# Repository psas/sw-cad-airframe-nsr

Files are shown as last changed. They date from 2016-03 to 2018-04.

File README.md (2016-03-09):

# Nosecone Separation Ring: The NSR

Solid Works CAD files and history of the nosecone separation ring

See https://github.com/psas/sw-cad-common#psas-solidworks-setup-and-use-procedures for procedures on using github for Solidworks files

## Documentation

Old docs from ancient wiki:

### <http://psas.pdx.edu/LV2cNoseconeSeperationRing/>

 - Drop test: <http://psas.pdx.edu/news/2009-04-19/>
 - Early deploy tests: <http://psas.pdx.edu/news/2009-03-15/>

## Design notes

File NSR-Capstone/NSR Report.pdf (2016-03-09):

# Nose Cone Separation Ring for LV3 High Altitude Sounding

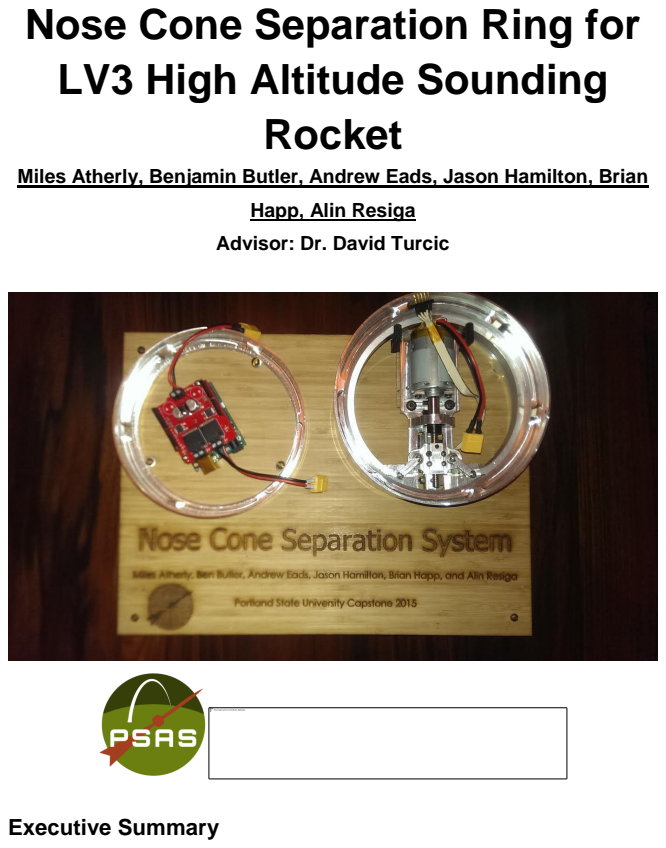
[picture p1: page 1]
Rocket; Executive Summary

Miles Atherly, Benjamin Butler, Andrew Eads, Jason Hamilton, Brian

Happ, Alin Resiga
Advisor: Dr. David Turcic

An electro-mechanical Nosecone Separation Ring (NSR) system was developed for

Portland State Aerospace Society (PSAS). The electro-mechanical NSR will replace

PSAS’ current NSR mechanism, which uses a bonding agent and gunpowder charges.

The new NSR will address several shortcomings exhibited by the current separation

device.

The electro-mechanical NSR uses a DC motor, linear guide rail, ¼-16 ACME power

screw, and relative motion arms, guide pins, and rails to actuate an aluminum v-shaped

clamping band over two angled surfaces A wave spring, which provides a kickoff force

upon separation, is inlayed into a groove in the larger (male) coupling ring. Currently,

the prototype NSR is controlled by pulse width modulation (PWM) via an Arduino Uno

R3. Two limit switches control fore and aft travel of the sled during actuation, and cut

the power to the motor. In its current design state, the NSR is capable of deploying in

less than 63 milliseconds.

Physical testing, finite element analysis, and mathematical models were used to verify

reliability of critical components in the new NSR system. The most critical component,

which also bears the highest stress during actuation, is the aluminum clamping band.

The design of the band was optimized so that it has a minimum factor of safety of 1.67

throughout the actuation.

Table of Contents | Page
1.0 | Introduction | X
2.0 | Mission Statement | X
3.0 | Main Design requirements | X
4.0 | Top-Level Design Decision

5.0 | Final Design | X
6.0 | Evaluations of Components
6.1. V-Band Sizing and Analysis
6.2. Clamped Surface Analysis
6.3. | Motor Sizing | X
7.0 | Evaluations as Related to PDS | X
8.0 | Conclusions and Recommendations

Acknowledgements

Bibliography

Appendix A: Detailed Design

Appendix B: DFMEA on V-band

Appendix C: Potential Yielding at Critical Point

Appendix D: Bill of Materials

Appendix E: Analysis Based Design Decisions

Appendix F Assembly Instructions

Appendix G: Drawings

## 1.0 Introduction

Portland State Aerospace Society (PSAS) was founded in 1997 with the goal of putting

a nano-satellite into orbit. PSAS is in the process of building their third sounding rocket,

and is redesigning several aspects of this rocket, including the nose cone separation

mechanism. Currently, the nose cone is adhered to the main body of the rocket with

epoxy. A small amount of gunpowder is deposited throughout a cavity between the

nose cone and body. At apogee, the gunpowder is ignited via electric matches,

breaking the bond of the epoxy. An internal plunger assembly then pushes the nose cone off the rocket, deploying the parachute. This separation method is not easily

testable, but does allow the rocket to be recovered and reused. PSAS would like an

easily testable, reliable, and more efficient way of releasing the nose cone and

deploying the parachute. Ideally, the new parachute deployment mechanism would be

easy to reset and not use any consumables, such as gunpowder.

Four main separation mechanisms were used to draw ideas from. A Marmon clamp, a LightbandTM, gas actuated pins, and an electromagnetic lock. An electro-mechanical

device similar to the Marmon Clamp, and the V-Band, was chosen for its simplicity and

reliability. The design relies on the expansion and contraction of an angled band to

clamp the upper and lower rings of the rocket together. This device increases the

diameter of the clamping band using a power screw driven by a motor. Since the power

screw is self-locking, the two rings stay clamped without additional power. The motor

reverses the direction of the power screw, and the rings become unclamped in under 63

milliseconds. The electro-mechanical NSR meets all of the design requirements; it is

easily resettable, easily testable, and will withstand the forces it will experience in flight.

## 2.0 Mission Statement

The mission of the NSR team was to design and prototype a device that will facilitate

the separation of the nose cone from the main body of the rocket. The device needs to

be easily testable, resettable, and have a failure rate of less than one percent. The

device must not impede the parachute deployment, and needs to be completed by

June, 5, 2015 with a budget of $3,000.

## 3.0 Main Design Requirements

The current NSR cannot be tested without firing the gunpowder charges which makes it

difficult to predict if the separation ring has been prepared correctly before launch. The epoxy used to bind the nose cone to the body takes several hours to cure, so if any

problems are detected before launch they cannot be corrected on the same day. PSAS

would like to replace their existing NSR with an electro-mechanical device that can be

tested, easily reset, and have a verifiable failure rate of less than one percent. This

would allow them to check the NSR mechanism on launch days. If the device were to

fail, it needs to fail in the closed position (i.e.-the nose cone remains attached to the

airframe in the event of system failure). This is significantly safer than failing in the open

position (i.e- the nose cone is detached from the airframe in the event of system failure)

The NSR should use no more than 5W of standby power and no more than 50W of

power to actuate from the main battery. The device also needs to be operable in a

vacuum, and withstand a tensile force of 250lb PSAS requested, but did not require

that the design of the NSR be modular and scalable so that it can be adapted for stage

release applications and for larger diameter rockets in the future.

## 4.0 Top-Level Design Decision

The three main concepts that were pursued were an electro-mechanical device driven

by a stepper motor, a compressed gas powered 4- pin actuator, and an electromagnetic

lock. The gas powered 4-pin actuator was discarded due to difficulties designing it to fail

in a closed position. An electromagnetic lock design was quickly discarded because the

magnets could be damaged upon touchdown impact. Ultimately, the decision was made

to use a clamp similar to the V-band and Marmon clamp driven by a DC stepper motor.

Later, the stepper motor was replaced with a brushed DC motor as it is easier to

manipulate, can be over-driven, and will satisfy the speed and power requirements of

the proposed design.

From the external and internal search, a concept scoring matrix was used to decide

between alternative ideas. The results are summarized in Table 1. The V-band has the

highest score, and was used as a starting point for the NSR design.

Table 1. Concept Scoring Matrix: Larger numbers correspond to more desireable qualities

| V-band | LightbandTM | Gas Actuated Pins | Electromagnetic
Speed | 3 | 3 | 4 | 5
Manufacturing Complexity | 4 | 3 | 3 | 2
Power System | 4 | 4 | 2 | 2
Binding Risk | 4 | 3 | 2 | 4
Totals | 15 | 13 | 11 | 13

The primary reason for designing a mechanism similar to the V-band instead of something more similar to the LightbandTM was due to manufacturing complexity. The

LightbandTM uses a series of right angle clamps to hold down the upper ring. These

clamps are fixed to the bottom with a shear pin. Creating this design would involve

sourcing or machining eight to ten of these right angle clamps, and designing a way to

fixture them to the lower ring. Having all of these components might also increase the

risk of loading failure. For example, the shear pins could break or the top part of the

right angle clamp could shear off. The decision was also made to clamp from the inside

instead of the more traditional style of clamping from the outside to keep the rocket as

aerodynamic as possible. Figure 1 is a cut-away model of the design where some of

the design aspects are seen..

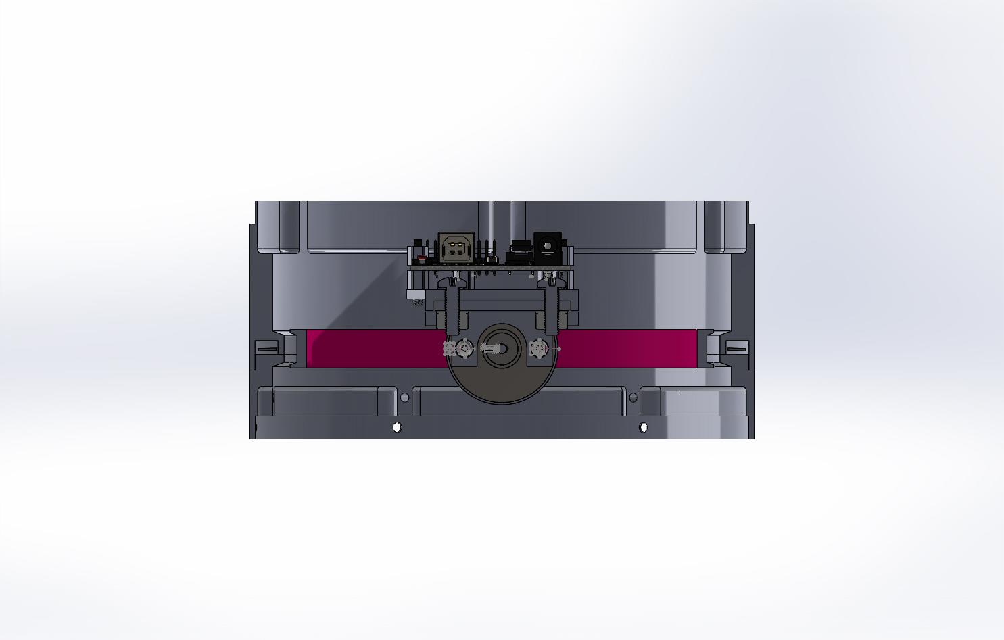
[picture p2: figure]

Figure 1- An isometric cut-away view of the initial design proposal. The design incorporates aspects of both the Marmon Clamping System and the LightbandTM separation device.

The NSR design utilizes an internal inverted marmon clamp. The actuation of the inverted marmon clamp works similarly to the LightbandTM in that the actuation is started

by translating rotational motion from a DC motor into linear motion. The similarities

between the two devices end there, as the NSR’s clamping mechanism significantly differs from that of the LightbandTM.

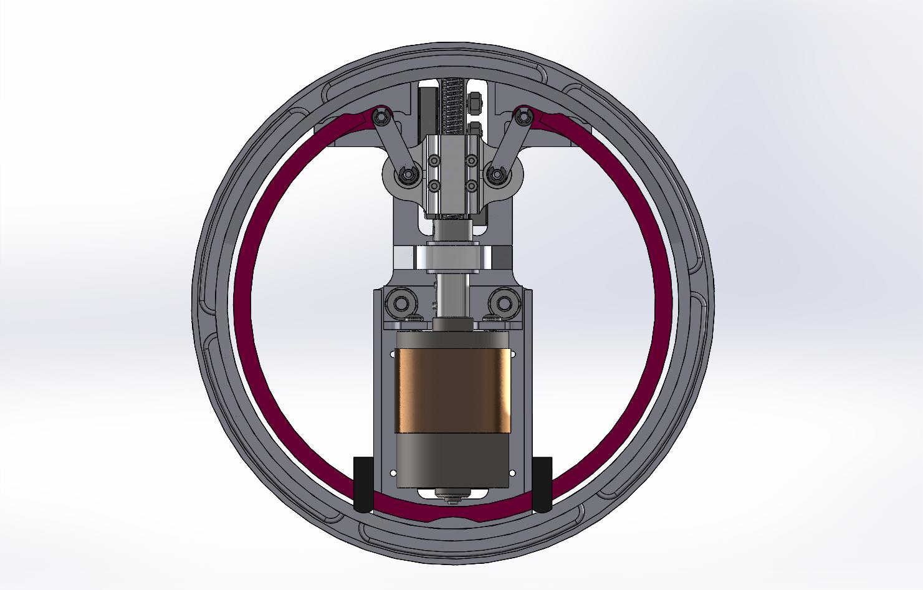
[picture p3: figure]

Figure 2- Top down view of the separation mechanism.

## 5.0 Final Design

The purpose of the mechanism is to provide a clamping force from the V-band

simultaneously to the upper and lower rings to hold the nose cone to the rocket during

flight. Then, at the desired point in flight, release the nose cone and deploy the

parachutes by rapidly contracting the V-band. The nose cone is attached to the upper

coupling ring (female) and the main body of the rocket is attached to the lower coupling

ring (male).

The NSR mechanism is powered independently by an 11.1 V Lithium Polymer

battery. Actuation is started by sending a signal from the flight computer to the control board which powers the motor and drives the V-band to either an open or closed

position. The power screw rides on and is supported by the journal and a pair of needle

thrust bearings. The sled rides back and forth along the power screw, which provides

two important functions; direct horizontal motion for sliding the V-band forward or back

to either clamp or release the nose cone, and to actuate the relative motion arms to

open or contract the V-band.

During the clamping or unclamping sequence, the sled will contact one of two

limit switches mounted under the device. The limit switches signal the control board to

stop the motor and end the actuation sequence. The actuator is attached to the upper,

larger, coupling which will be attached to the nose cone. Upon deployment, the

actuator will separate from the rocket body with the nose cone, allowing plenty of space

for the drogue and main parachutes to deploy through. Figure 3 is a bottom up view of

the complete NSR mechanism. Not pictured are the arduino and the battery.

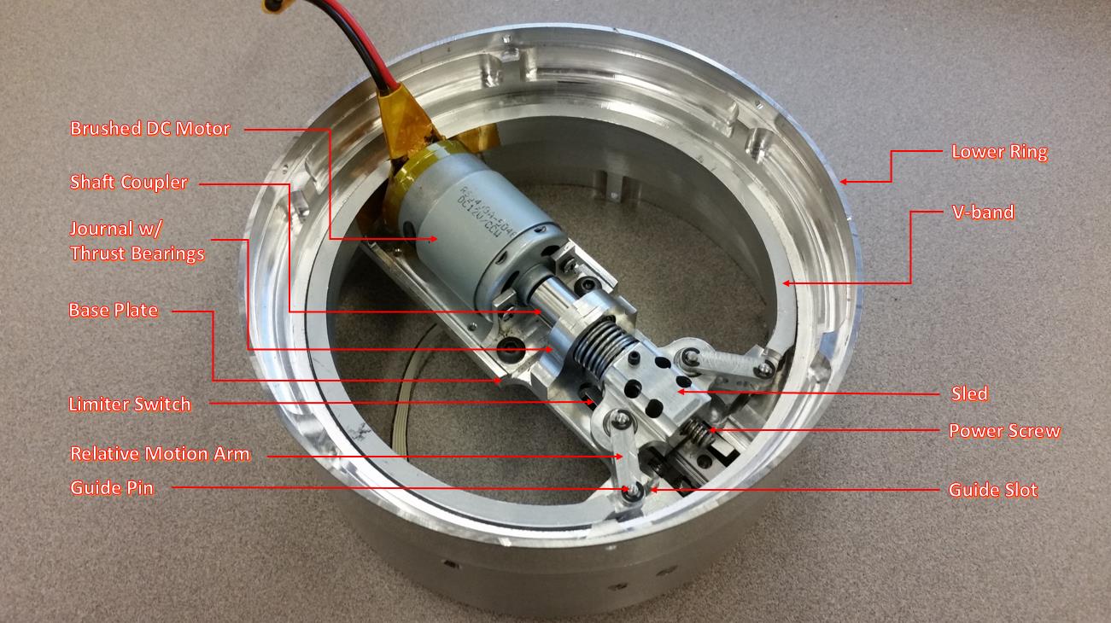
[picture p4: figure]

Figure 3: A bottom up view of the complete NSR assembly.

The NSR components are a combination of in-house custom manufactured components

and prefabricated outsourced components. The in-house manufactured components include both coupling rings, V-band, journal, shaft coupler, sled, motor mount, dowel

pins, male indexing tabs, and actuator arms. The outsourced parts include the power

screw, thrust bearings, 7mm guide rail, 7mm carriage, motor, control board, LiPo

battery, wave spring, and all fasteners.

## 6.0 Evaluation of Components

After the final design concept was approved, three major design points of the NSR were

evaluated. The three design points are the V-band, the clamped surface area of the

coupling rings, and the power requirements of the system.

## 6.1 V-Band Sizing and Analysis

A mathematical model constructed using Castigliano’s theorem, shown in Appendix

E,shows that the force required to displace the tabs of the band depends heavily on the

radius of curvature and the cross-sectional area of the band. The force required to

displace the band will be reduced by increasing the radius of curvature of the neutral

axis, or by decreasing the cross-sectional area of the band. The original V-band design

required a load of 10 lbf per side (20 lbf total) to achieve a net displacement of 0.8 in.

To determine the stress present in the displaced state of the V-band, an FEA model of

the band was built and subjected to a similar load. Meshing properties of the FEA

model were adjusted until the force and displacement parameters of the FEA model

resembled the force and displacement parameters for the mathematical model.

Additionally, a physical experiment was performed in order to validate the results of both

the FEA and the mathematical mode, shown in Appendix C. Results from the physical

experiment matched results from the FEA model and the mathematical model closely,

and the FEA model was deemed as a viable design tool for optimizing V-band

parameters.

FEA analysis of the original V-band exhibited a maximum stress value of 36.98 kpsi

located on the back side of the band on the lip of the clamping surface illustrated in

Figure 4. Since the yield strength of 6061-T6 aluminum is 40 kpsi, the original V-band

design had a factor of safety of 1.08 in its deployed state. A design revision of the V-

band was done in order to increase the factor of safety of the band in the deployed state

as well as decrease the force required for displacement. FEA was used as the primary

design tool in this process.

The cross-sectional area of the V-band was thinned out significantly by removing

material from the web and the lips of the clamping surface. The center of the V-channel

was held constant in order to shift the radial distance of the neutral axis outwards.

Thinning the web and removing material from the lips of the clamping surface reduced

the force required to displace the band from 20 lbf to 6.6 lbf, but did not significantly

reduce the maximum observed stress value. 1.5 in diameter relief cut was added to the

back wall of the V-band where the maximum stress was observed. The addition of the

relief cut reduced the observed stress to 23.92 kpsi and increased the factor of safety to

1.67. The completely revised V-band is seen in Fig. 5 and shows the maximum stress

concentration location, and magnitude relative to yield strength of the material.

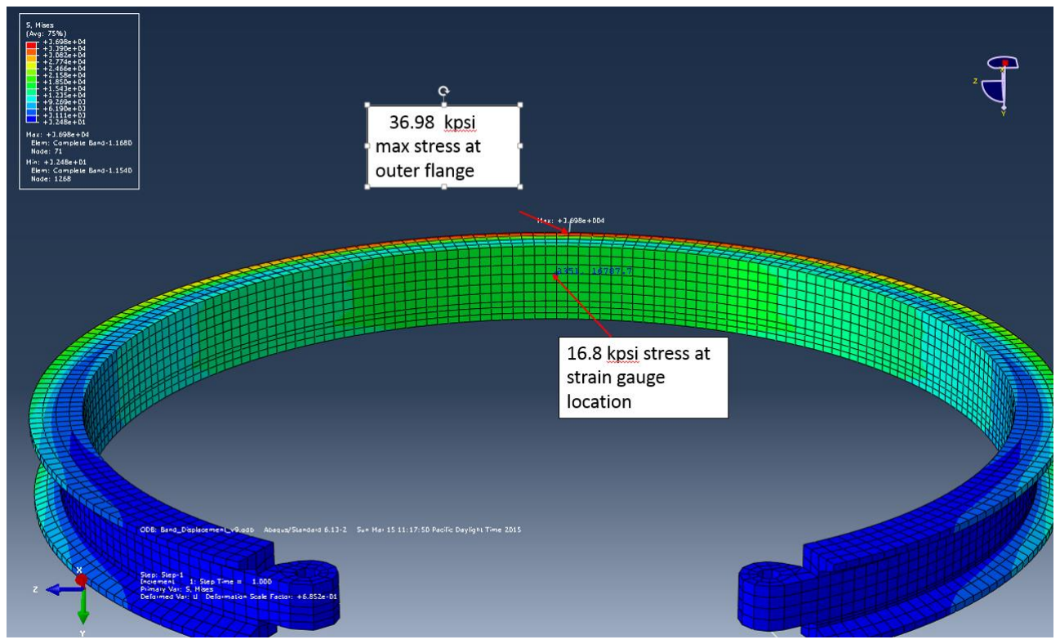
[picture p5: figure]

Figure 4: FEA analysis of the location and magnitude of maximum stress concentration.

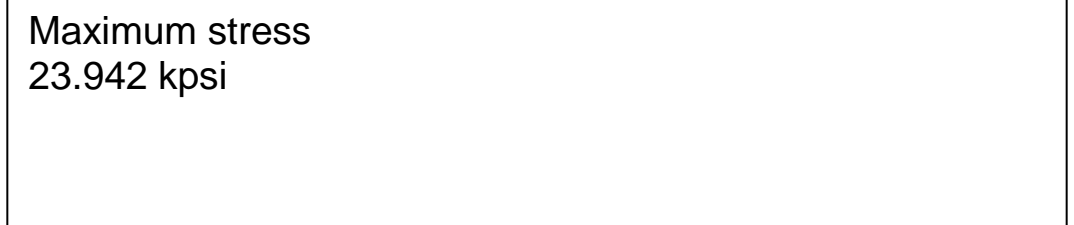
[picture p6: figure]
Maximum stress 23.942 kpsi

Figure 5: Maximum stress relative to material yielding with smaller webbing and a relief cut.

## 6.2 Clamped Surface Analysis

Figure 6 shows the cross sectional area that the V-band clamps to inside of the coupling

rings. The designed cross sectional area was analyzed using an axial load of 250 lbf in

order to determine if the clamped surfaces will yield. The minimum theoretical cross

sectional area requirement was calculated to be 5.873 ∗ 10

−3
in

2
. Figure 6 shows the

smallest designed cross sectional area of the clamped surface of 0.0128 in

2which will

not yield at the theoretical axial load and is ideal as the large cross sectional area adds

robustness. For the complete analysis of these design dimensions see Appendix E.

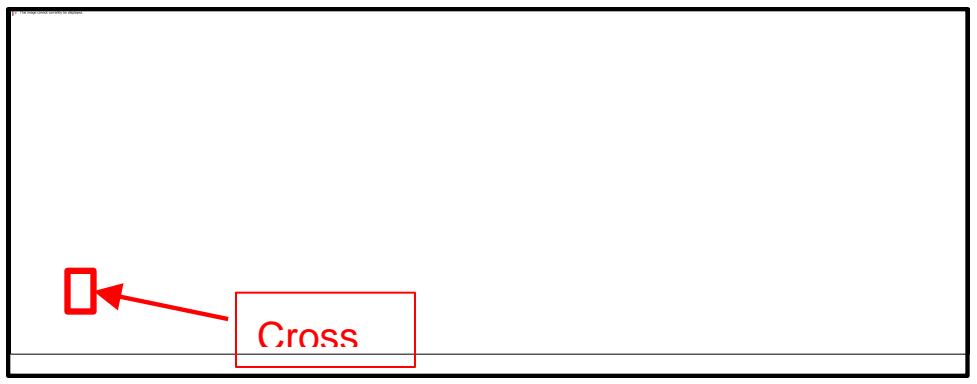
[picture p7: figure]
Cross

Figure 6: Smallest cross sectional clamping area analyzed for yielding

## 6.3 Motor Sizing

To accurately size the motor, a torque test on the power screw was performed. To

determine the amount of radial deflection the power screw will experience under specific

torque loads, and to develop a method to characterize a torque curve for the power

screw, a strain analysis was performed on a ¼” steel rod similar in size and material to

that of the power screw. The ¼” rod stock seen in Figure 7 with the attached strain

gauge was used in lieu of the power screw due to size and shape constraints for

applying the available strain gauge to the power screw. The validated torque testing

method was then going to be applied to the power screw to determine the maximum

torque needed to actuate the V-band. However, the strain gauge method was not used

due to difficulties in applying a strain gauge to the turned down ⅛” round end of the

power screw. The maximum torque required to actuate the V-band was determined to

be to be approximately 3 in-lb. The maximum torque was found by measuring different

loads applied to the end of a radial arm which was attached to the power screw in the

prototyped model. The load required during the last 1/8th turn of the power screw was

taken to be the maximum required torque. The maximum determined torque value was

multiplied by safety factor of to 2 to ensure the selected motor had enough capacity to

actuate the V-band within the time limit outlined in the PDS.

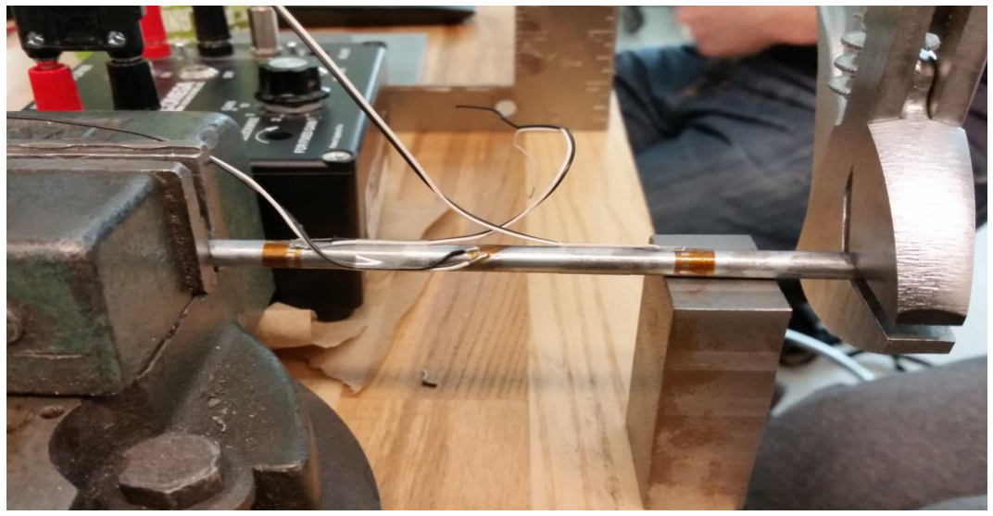
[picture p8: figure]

Figure 7: Torque testing on the ¼” rod stock used to validate the torque testing method.

## 7.0 Evaluations as Related to PDS

The main requirement from PSAS is that the system can be easily reset and quickly

tested. The design meets this requirement, and can be actuated and reset several times

per minute. The device has an actuation time of 63 milliseconds.

By designing the NSR such that the motor and baseplate assembly are attached to the

nosecone, two requirements were met. The parachute can deploy without interference

from the device, and there is now room to attach an independent battery. The device

requires no power from the main rocket battery, satisfying the power requirements

outlined in the PDS.

Using FEA, both loading requirements were verified. See Appendix C for the results.

The inside band can withstand the 250lb tensile force with a factor of safety of 30.

As seen in Appendix C, the stress on the V-band is 24 ksi at full actuation. According to

Equation 1, the V-band can be fully actuated and brought to rest 44,000 times before

being affected by fatigue.

N = [2,100,000/(S − 14,000)]

2
(1)[9]

Where N is the number of cycles until failure and S is the stress on the part (24 ksi).

The budget for this project was $3,000. Because most of the machining was done in-

house, the final product was made at a fraction of the total budget. The final cost of

production was $1,300.

## 8.0 Conclusion and Recommendations

An alternative NSR device that does not use consumables, such as epoxy and

gunpowder, was developed by the June 5th deadline for a total cost of $1,300. The

system utilizes a unique internal V-band design to apply a clamping force to two

customized coupling rings that will be mounted on the LV3 rocket. The new NSR is

robust in design. FEA shows that the NSR will be able to sustain tensile loadings of up

to 250 lbf with a factor of safety of 30. Fatigue analysis on the V-band shows that it will

sustain 44,000 cycles of actuation before failure. The actuation time of the NSR is 63

milliseconds (conservatively), so the device can be tested and reset several times a

minute. The system is equipped with its own power source and will not draw more than

a nominal amount of power from the main rocket battery. The system is designed to fail

in the closed position as requested.

Designing the electro-mechanical NSR presented several unique challenges. The size

of the LV3 rocket modules limited the type of actuators that could be used. Designing a

clamping system that utilizes bending in key components is unorthodox in nature. The

power requirements of the system were such that a custom drive train had to be

designed and machined.

A prototype electrical system utilizing an Arduino Uno R3 and a 30 Amp H-Bridge was

developed to test the new NSR system. Controlling the system for position and speed

has proven to be difficult due to the extremely fast wind up of the motor and the small

linear displacement of the actuator. The stall current of the motor is 85 Amps and the no

load speed of the motor is 19300 RPM. The use of the 30 Amp H-Bridge limits the

motor from operating over its full torque range. The lack of low end power due to the 30

A current ceiling sometimes causes the system to become bound in the forward

position. Additionally, the sampling rate of the Arduino Uno is limited to 9600 samples

per second. When the NSR is actuating, the motor spins up so fast that the system has

a tendency to overshoot the fore and aft limit switches before the power to the motor is

braked to the ground pin of the Arduino. This makes the system very difficult to

precisely control. The system would benefit from using a faster control board that is not limited to an amperage below the motors stall current. Additionally the NSR system

would benefit from a second type of feedback other than limit switches to avoid binding

in the forward or reverse position. A pressure sensor, force transducer, proximity

switch, or a more advanced position detection system could be implemented to improve

the performance and reliability of the device.

## Acknowledgements

The Nosecone Separation Ring group would like to give special acknowledgement to

Jeffrey Hickman, Dr. Turcic, Mike Chuning, Andrew Greenberg, Nathan Bergey, Gavin

Gallino, Sam Stewart, and all the members of PSAS for their support in this project.

## Bibliography

[1] Budynas, Richard G, J K. Nisbett, and Joseph E. Shigley. Shigley's Mechanical Engineering Design. New York: McGraw-Hill, 2011. Print.
[2] Dailey, J., 2014. AFRL Technology Demonstrated on NASA Moon Mission. [Online] Available at: http://www.wpafb.af.mil/news/story.asp?id=123418650
[Accessed 8 January 2015].
[3] Dirgo, B., 2013. Orbital Sciences Corporation Payload Separation System. [Online]
Available | | at:
http://www.cefns.nau.edu/capstone/projects/ME/2014/OrbitalPayloadSeparationSystem/images/carosel_images/4_new.png
[Accessed 25 November 2014].
[4] Lazansky, C., 2012. Refinement of a Low-Shock Separation System, s.l.: s.n.
[5] NASA, 1970. Flight Separation Mechanism, s.l.: s.n.

[6]NASA, n.d. Marman Clamp System Design Guidelines, s.l.: s.n.

[7] NEA Electronics Inc., n.d. Ensign-Bickford Aerospace & Defense. [Online]
Available | at: | http://www.eba-d.com/assets/product-sheets-nea/V-Band-Product-
Sheet.pdf
[Accessed 8 January 2014].
[8] Sierra Nevada Corporation, n.d. Qwksep Payload Separation System. [Online]

Available | at:
http://www.spacedev.com/pdfs/Qwksep%20Payload%20Separation%20System.pdf [Accessed 8 January 2015].
[9] Yahr, G. T., 1993. FATIGUE DESIGN CURVES FOR 6061-T6 ALUMINUM, Oak Ridge, Tennessee: Oak Ridge National Laboratory.

## Appendix A: Detailed Design

The LV3 launch vehicle is composed several modular sections that have an inner

diameter of 6 inches and an outer diameter of 6.6 inches. The inner diameter of the

modular sections was a major design constraint and was used as the starting point for

the NSR design. Castigliano’s theorem shows that for a curved beam, the force

required to deflect the beam a set distance is dependant on the radius of curvature of

the neutral axis of the beam and the cross-sectional area of the beam. Castigliano’s

theorem was initially used to design the V-band such that the force required to actuate

the band within the 6 inch diameter modules would be at a minimum. The clamping

surfaces onto which the V-band mated were fixed at 5.7 inches in diameter. A 20

degree angular clamping surface was decided upon, because the angled surface helps

guide components into proper placement during mating. The height of the V-band was

fixed at 0.5 inches. Single part FEA of the V-band and the clamping surfaces showed

that all surfaces could sustain t a 250 lbf tensile load with a factor of safety of 30. FEA

was later used to optimize sizing parameters of both the V-band and the coupling ring

clamping surfaces.

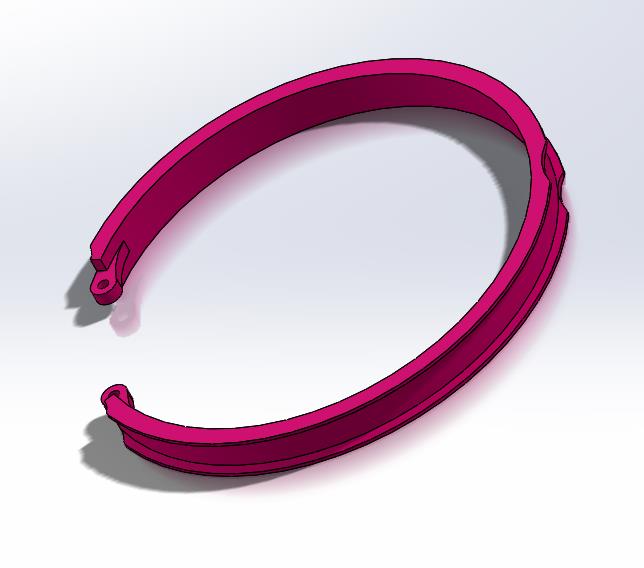
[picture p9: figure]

Figure 1A- Final V-band design.

Actuation of the V-band requires that a pair of equal and opposite forces be applied to

the two tabs of the V-band. In order to accomplish this, a linear actuator needed to be

designed. FEA, Castigliano’s theorem, and real world experimentation showed that a

minimum force of 8 lbf per tab was needed to actuate the band. The force requirement

combined with the space constraints of the LV3 modules immediately disqualified many

traditional prefabricated linear actuators. In order to satisfy the power requirements of

the V-band, a high powered brushed DC motor and custom linear actuation mechanism

were needed.

A power screw was selected as a the preferred method of translating rotational motion

to linear motion. In order to keep the torque on the power screw low, a small diameter

(0.25 inch) screw was selected. A 7mm precision guide rail and carriage was selected

to provide a linear motion constraint to the actuation system. The guide rail is made out

of hardened steel and has a dynamic load capacity of 300 lbf. A sled and arm assembly

which interfaced with both the carriage and the V-band tabs was designed to transmit

the force from the DC motor to the V-band. During actuation, the arms of the sled are

allowed to rotate. The sled was fitted with ⅛” ID x ⅜” OD x 5/32” height ball bearings

which limit the friction incurred in the arms during actuation.

In order to mate evenly around the entire clamping surface, the center of the V-band

must be held constant while the diameter of the band increases. This was

accomplished by designing a set of relative motion channels which constrain the motion

of the V-band tabs (and sled arms) to a set path. The principles of rigid body kinematics

were used to describe the path the arms were required to follow in both rotation and

translation.

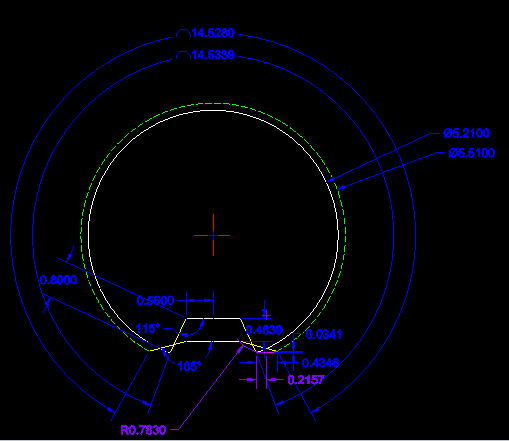
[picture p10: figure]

Figure 2A- A graphical representation of the V-band in its “open” and “closed” state. The

initial and final angle of the relative motion arms (yellow), and sled (white) are shown.

Additionally, the V-band perimeter is shown (solid white, dotted green).

A theoretical torque curve for the entire system was modeled using the required

actuation force, sled dimensions, rail dimensions, and power screw dimensions. The

model predicted that 6 lbf-in of torque was needed to actuate the power screw. The net

linear distance traveled by the sled to accommodate full actuation was found to be

0.4636 inches. This distance corresponds to just over 4 complete rotations of the ¼-16

ACME power screw. A motor that was capable of delivering the determined torque

requirements as well as the goal actuation time of 0.1s was selected. The dimensions

of the selected motor allowed for direct drive of the device.

A base plate was designed to incorporate all of the above mentioned elements as well

as two slots for limit switches. The base plate bridges the 6 inch diameter of the

coupling rings for added strength and stability. Single part FEA of the baseplate showed that it could sustain a 250 lbf concentrated load applied to the part center. The

base plate design also includes a 1.5” x 1.5” pattern of 4-40 tapped mounting holes onto

which a control board or control board adapter can be mounted. The base plate is held

in place with seven 4-40 tapered machine screws which interface with the coupling

rings. A modular stem was designed to mount to the bottom of the baseplate. The

modular stem adds additional structural stability as well as providing a surface onto

which limit switches and other feedback mechanisms can be mounted.

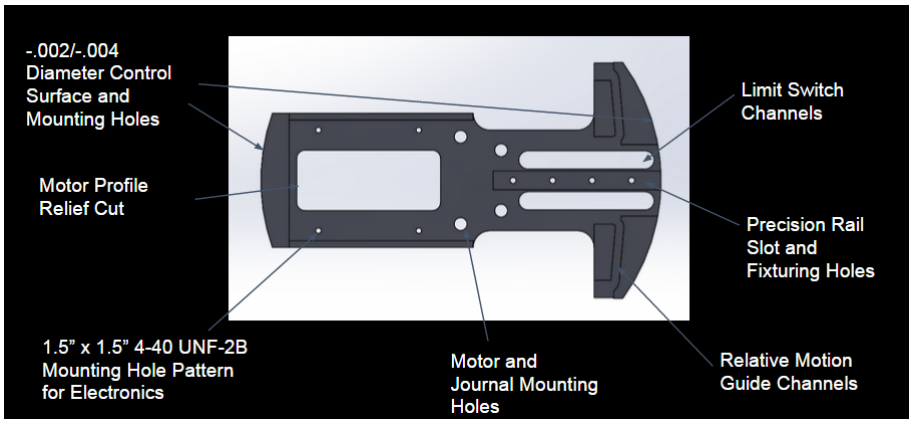
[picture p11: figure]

Figure 3A- Baseplate design showing many of the mentioned design features.

A pair of custom coupling rings was designed to interface with the NSR actuator and V-

band. The male coupling ring is indexed with three female half inch alignment grooves

around the surface which mates to the female NSR coupling ring. The female coupling

ring contains 3 male tabs which interface with female grooves as well as holding a wave

spring in place. The wave spring provides a kick-off force of approximately 88 lbf upon

actuation. Both coupling rings have an outer diameter of 6.6 inches and an inner

diameter of 6 inches outlined in the PDS. The coupling rings also exhibit the same

internal structural features as the standard LV3 coupling ring modules and can thus be

fitted to any standard LV3 coupling ring. This allows the NSR device to later be adapted

to stage separation if PSAS decides to do so.

Figure 4A- A cutaway view of the NSR assembly including coupling rings and wave

spring.

A prototype control system utilizing an Arduino Uno R3, a pair of limit switches, a button

and a Monster Moto H-Bridge was developed for testing and demonstration purposes.

The control system continuously samples a set of input pins for a state change to occur

in the button. If a state change is sensed, the controller checks the status of each limit

switch to determine the current position of the V-band. When the position has been

detected, the controller then drives the motor in the direction needed to move the band

toward the opposite limit switch. The controller then monitors the input pins for a

second state change corresponding to the activation of the new limit switch. When the

switch has been activated, the control board brakes the motor to the ground pin of the

motor shield and control board.

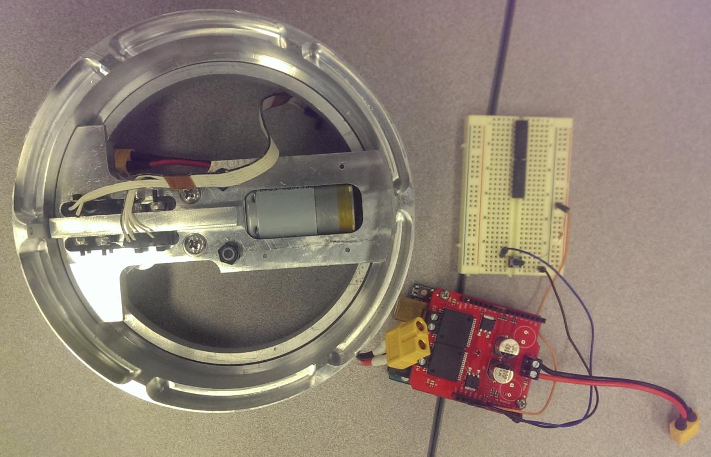
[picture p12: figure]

Figure 5A- Prototype control system of the NSR.

## Appendix B: DFMEA on V-band

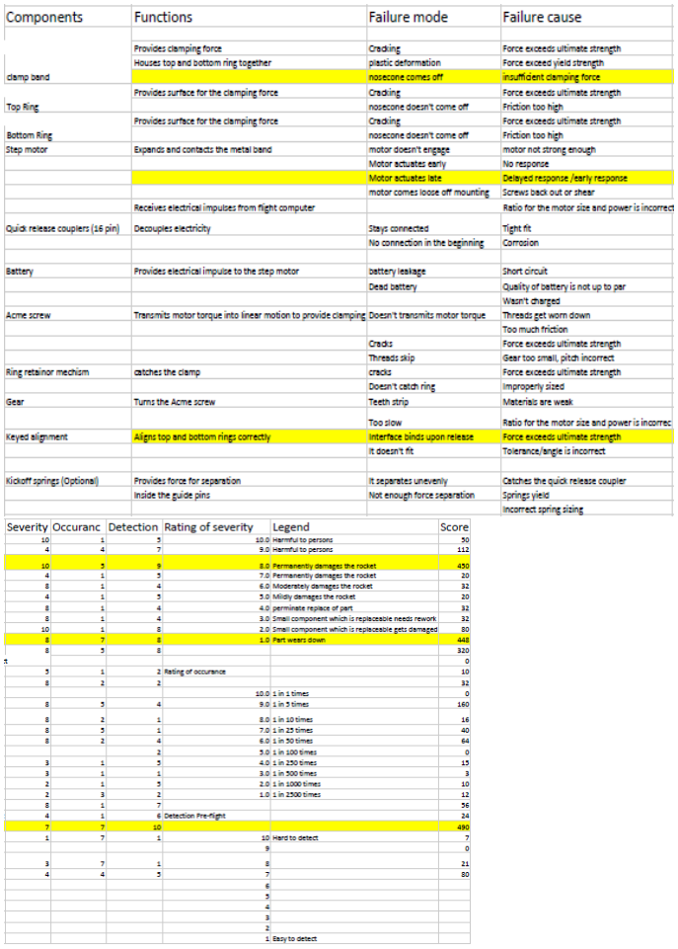
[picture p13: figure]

Figure 1B: The DFMEA on the V-band which shows the three most critical failure modes.

## Appendix C: Potential Yielding at Critical Point

A circular aluminum clamping mechanism (V-band) was tested to determine the force

required to displace the band. A strain gauge was also mounted to the inside of the band to measure stress at a critical location. This location was chosen because it was

determined as the most critical point in the V-band. Stresses and displacements in the

band were analysed prior to conducting the experiment using Abaqus Finite Element

Analysis (FEA) software. The software was also used to determine the force required to

displace the V-band to the maximum diameter. This testing was important due to the

requirements brought by the PDS. The PDS requires the NSR to be quick to reset and

quick to test, therefore the FEA software will tell the group the required forces and any

possible yielding stresses in order to clamp the rings fully.

The dimensions, material, and change in clearance was known. The force and stress at

critical points required to change the clearance 0.8 inches is desired to be known. There

were three methods which were used, FEA half band, FEA full band and Castigliano's

method. The main assumptions made were to try either the half band or the full band.

The results showed to be closed to the actually readings as depicted in Table 1C. The

experimental schematic could be seen in Figure 1C. While the two FEA analysis were

depicted in Figure 2C.

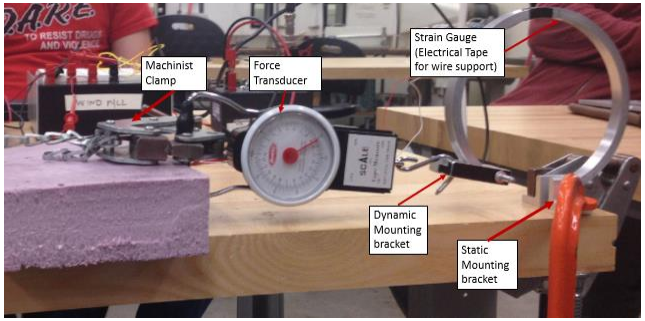
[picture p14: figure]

Figure 1C: The fixtures and apparatus of the experiment: note that the force exerted on the

dynamic end of the V-band was in-line with the static end; i.e. the motion was constrained in one

dimension. See appendix A for more details

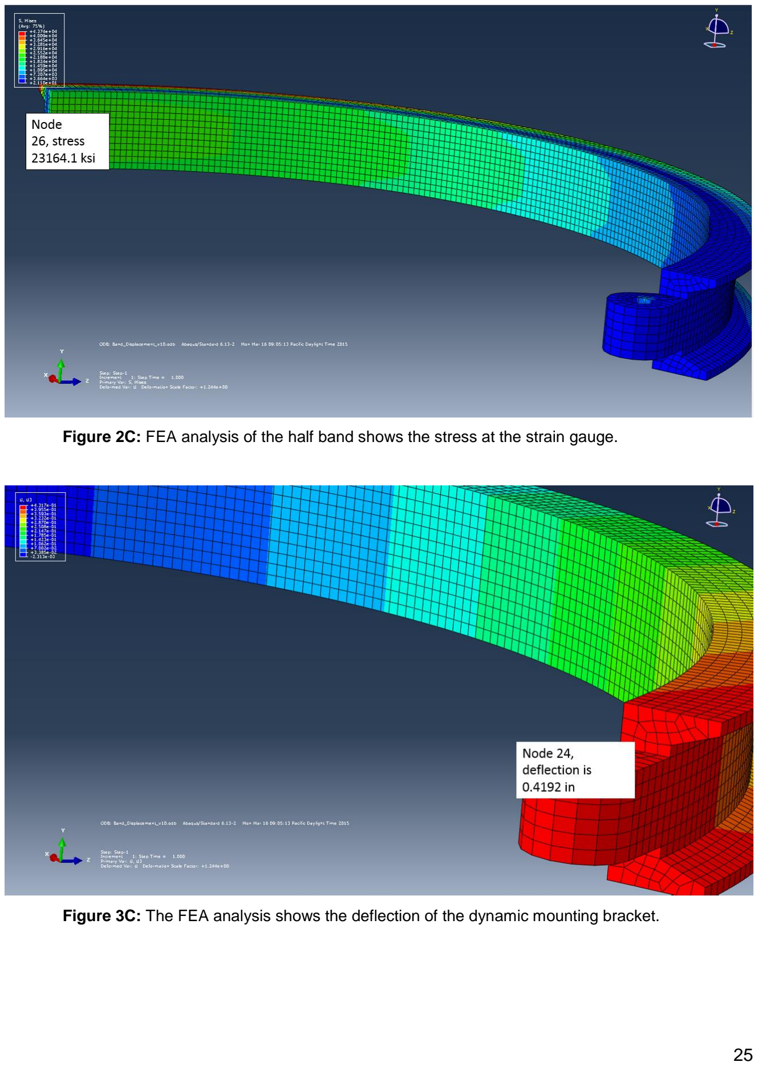
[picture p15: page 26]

Figure 2C: FEA analysis of the half band shows the stress at the strain gauge.

Figure 3C: The FEA analysis shows the deflection of the dynamic mounting bracket.

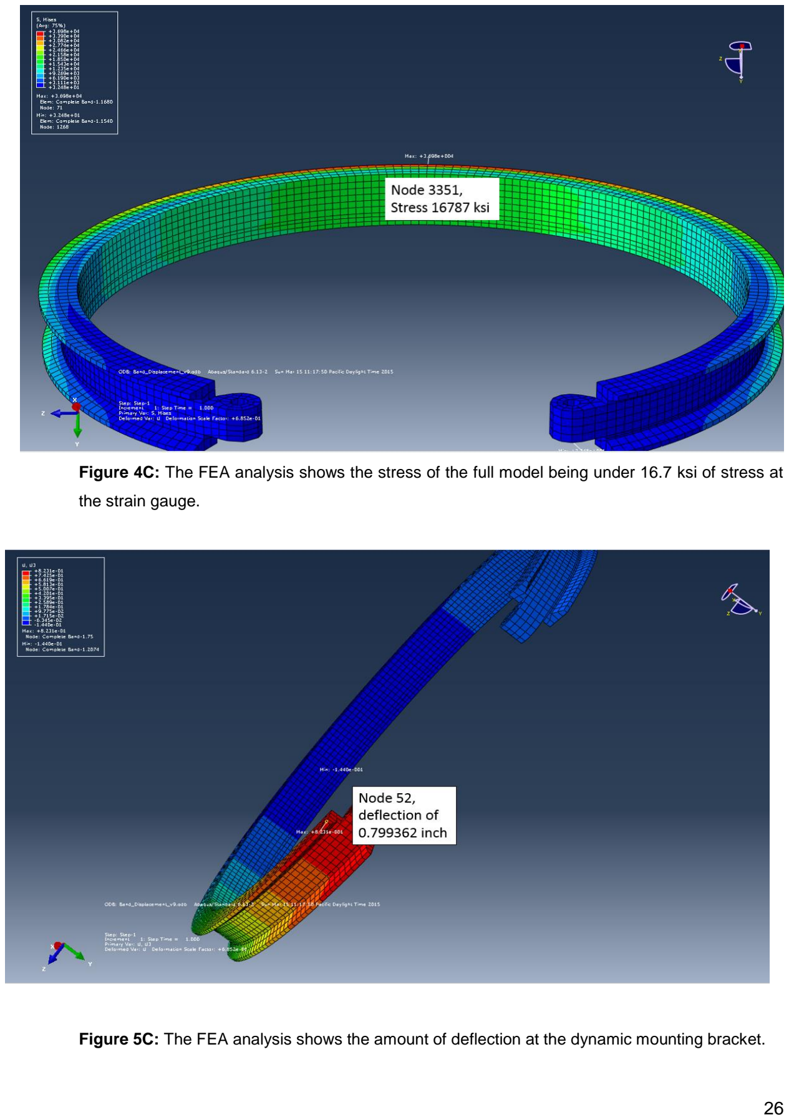
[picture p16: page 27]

Figure 4C: The FEA analysis shows the stress of the full model being under 16.7 ksi of stress at

the strain gauge.

Figure 5C: The FEA analysis shows the amount of deflection at the dynamic mounting bracket.

Table 1C: The force required and stress generated in deflecting the V-band 0.8 in.

| Experimental | Castigliano's method | FEA: Full V-band Geometry | FEA: Half V-band geometry
Force to deflect V-band 0.8 in. | 20.67 lbf | 15.69 lbf | 20.6 lbf | 15.7 lbf
Stress at strain gauge location | 27.90 ksi | N/A | 16.79 ksi | 23.16 ksi

Table 2C: Shows which methods had the lowest amount of error between each other in terms of force

(lbf)

Percent error force required for V-band displacement | Experimental | Castigliano’s method | FEA full geometry | FEA half geometry
Experimental | 0 | 24% | 0.3% | 24%
Castigliano’s method | 24% | 0 | 23.8% | 23.7%
FEA full geometry | 0.3% | 23.8% | 0 | 23.7%
FEA half geometry | 24% | 0.06% | 23.7% | 0

Table 3C: Shows which methods had the lowest amount of error between each other in terms of

stress (ksi)

Percent error stress | Experimental | Castigliano’s method | FEA full geometry | FEA half geometry
Experimental | 0 | N/A | 39.8% | 16.9%
Castigliano’s method | N/A | N/A | N/A | N/A
FEA full geometry | 39.8% | N/A | 0 | 27.5%

FEA | half
geometry
16.9% | N/A | 27.5% | 0

The full band matched Castigliano's method, however the FEA half band matched the

experimental reading better. Error was generated in multiple stages of the experiment.

There was error in the readings from two key instruments, the digital caliper and the

hanging scale. These instruments had an error of ±0.001 in. and ±0.5 lb. respectively.

Over three trials, the average force required to deflect the V-band 0.8 in was found to be

20.67 lbf, which agrees with a comparable FEA model.

## Appendix D: Bill of Materials

Shown below is a table listing all of the parts that are included in the final assembly.

Table 1D: Bill of Materials (BoM) for all parts included in the final assembly

Part | Description | Location | QTY
E clips | 1/8" E clips | Arms / sled, Arms / V-band | 8
M2 x 8mm socket | M2 x 8mm socket screw | Sled assembly | 4
7mm x 60mm rail | 7mm x 60mm length precision rail | baseplate assembly | 1
7mm carriage | 7mm clean room carriage | baseplate assembly | 1
1/8 x 3/8 x 5/32 bb | precision ball bearing | sled assembly | 2
6-32 set screw | 6-32 x .25 | sled assembly | 1
1/4-16 x .25 nut | ACME nut, 1/4/16 | sled assembly | 1
sled | custom machined sled | sled assembly | 1
2-56 x .5 panhead | 2-56 phillips panhead | baseplate assembly | 3

limit switches | snap-action limit switch | baseplate assembly | 2
3-56 x 1 socket | 3-56 x 1 socket screw | baseplate assembly | 4
3-56 washer | washer / spacer | baseplate assembly | 8
3-56 lock nut | 3-56 nylon lock nut | baseplate assembly | 4
modular stem | custom machined stem | baseplate assembly | 1
baseplate | custom machined baseplate | baseplate assembly | 1
.25 x .678 thrust bearing | INA needle thrust bearing, .25 | journal | 2
.25 x .678 thrust washer | INA needle thrust washer, .25 | journal | 2
.175 x .125 coupler | custom machined coupler | journal | 1
.25 collar | shaft collar | journal | 1
1/4-16 ACME all thread | power screw | journal / drive train | 2.5 in
journal | custom machined journal | journal | 1
RS-550 motor | Banebots RS-550 | motor assembly | 1
motor mount | custom machined motor mount | motor assembly | 1
M3 x 6mm | M3 x 6mm machine screw | motor assembly | 2
10-32 x 5/8 | 10-32 machine screw | actuator assembly | 2
10-32 x 3/8 | 10-32 machine screw | actuator assembly | 2
10-32 lock nut | 10-32 nylong lock nut | actuator assembly | 2
relative motion arms | custom machined arms | actuator assembly | 2
dowel pin size 1 | custom dowel pin, size 1 | actuator assembly | 2
dowel pin size 2 | custom dowel pin, size 2 | actuator assembly | 2
V-band | custom machined band clamp | actuator assembly | 1
wave spring | smalley SSR-0637 | coupling rings | 1
index tabs | custom machined tabs | coupling rings | 3
4-40 x .25 | 4-40 x .25 tapered machine | coupling rings | 3

| screws
male coupling ring | custom coupling ring | coupling rings | 1
female coupling ring | custom coupling ring | coupling rings | 1
4-40 x .5 | 4-40 x .5 tapered machine screws | coupling rings | 7

## Appendix E: Analysis Based Design Decisions

Castigliano’s For V-band

Summary: The objective of this analysis is to find the amount of force required to open the v-band sufficiently for full clamping. The analysis uses Castigliano’s theorem to find that 15.6lb of force is needed to open the band .8 in. These results are less than the experimental value and value found by FEA, but still within reason. [1]

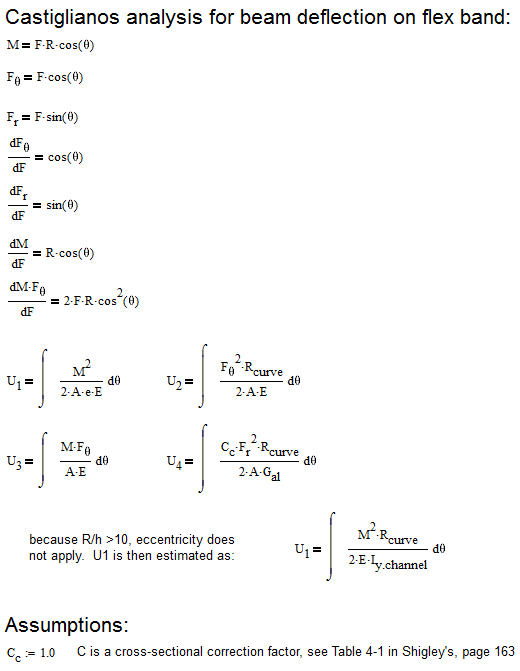
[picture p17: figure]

Calculating for yield of designed clamping area

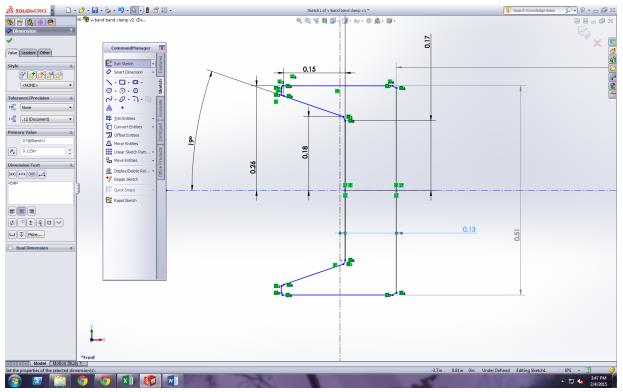
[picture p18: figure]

Figure 1E- Cross section of v-band.

Summary: The objective of this analysis is to find the minimum wall thickness of the V-band to withstand the forces outlined in the PDS. The PDS states that the device needs to withstand a minimum tensile force of 250 lbf.

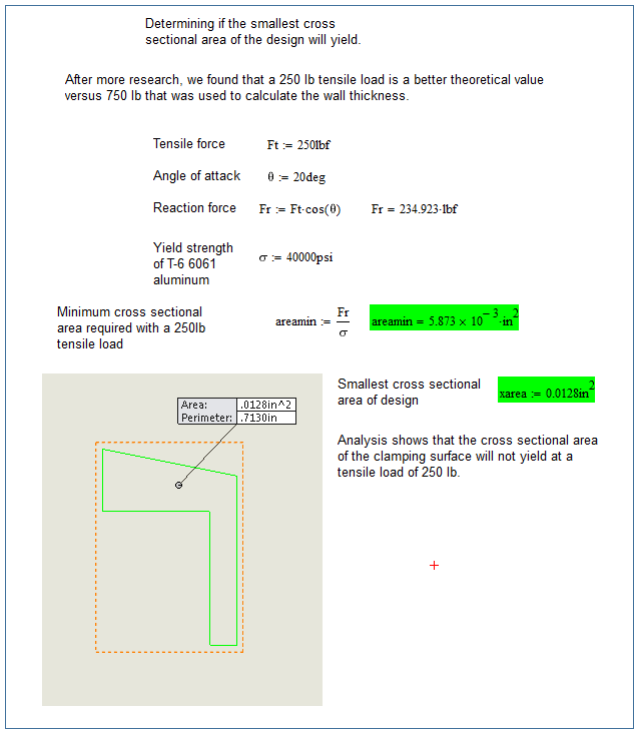
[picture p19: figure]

## APPENDIX F: Assembly Instructions

Sled Sub-Assembly

Part | Qty | Description
1 | 1 | Sled
2 | 2 | 1/8" ID x 3/8" OD Bearing
3 | 1 | 1/4-16 x .25" ACME Nut
4 | 1 | 6-32 Set Screw

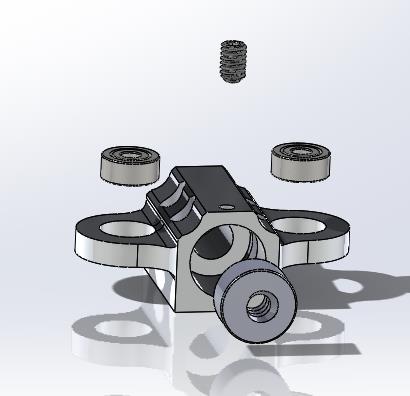
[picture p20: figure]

Instructions:
1. Using an arbor press, press both bearings into the holes along the side of the sled. Press the ¼-16 ACME Nut into the counterbore on the front surface of the sled.

2. Place some Loctite onto the threads of the 6-32 Set Screw. Screw the set screw through the hole located in the top of the sled until it is snug against the ¼-16 ACME Nut.

Baseplate Sub-Assembly

Part | Qty | Description
1 | 1 | Baseplate
2 | 3 | 2-56 x .5" Phillips Panhead Machine Screws
3 | 2 | Limit Switches
4 | 4 | #3 x 1" Socket Head Cap Screws
5 | 8 | #3 Nylon Lock Nuts
6 | 8 | #3 Washers
7 | 1 | 7mm x 60mm Precision Guide Rail
8 | 1 | Modular Baseplate Stem

Instructions:
1. Slide the 7mm Precision Guide Rail into the slot for the guide rail.
2. Place Modular Baseplate Stem on the bottom of the baseplate and attach the stem and rail using the 3 2-56 x .5” Phillips Panhead screws.
3. Align the rear limit switch with the left hand side of the Modular Baseplate Stem grooves as shown.
4. Thread two #3 screws with washers through the limit switch and Stem grooves. Place a second set of washers on the exposed end of the screws.
5. Thread two #3 Nylon Lock Nuts over the exposed ends of the screws. Tighten the nuts down most of the way, but leave some play in the limit switches for later adjustment.
6. Repeat steps 3 through 5 for the front limit switch, but with the switch facing the oposite way and in with the switch aligned to the forward most groove set of the Modular Baseplate Stem.

Drive Train Sub-Assembly

Part | QTY | Description
1 | 1 | Journal
2 | 2 | INA 0.25 ID x 0.688 OD Needle Thrust Bearings
3 | 2 | INA 0.25 ID x 0.688 OD Thrust Washers
4 | 1 | 0.125" x 0.125" Shaft Coupler
5 | 1 | 0.25" Shaft Collar
6 | 1 | 1/4-16 x 2.75" Length ACME Power Screw

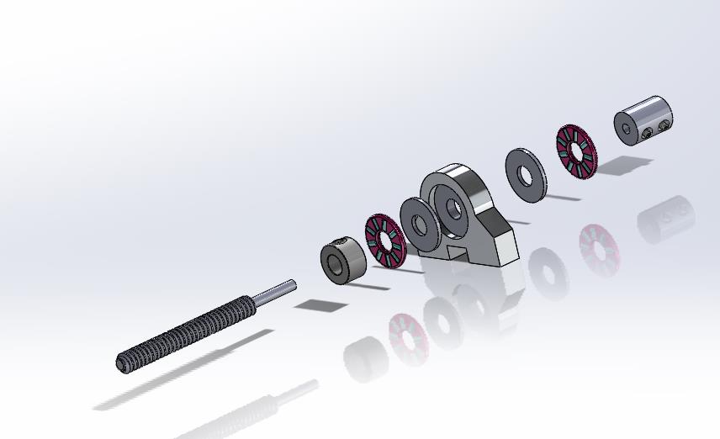
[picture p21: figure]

Instructions:
1. Seat one Thrust Washer and one Needle Thrust Bearing into the Journal.
2. Seat the 0.25” Collar onto the ACME Power screw approximately 2.25” down the shaft from the unturned side.
3. Slide the power screw through the journal and bearing assembly until the 0.25” Collar is seated against the Needle Thrust Bearing.
4. Repeat step one for the other side of the Journal.
5. Seat the 0.125” to 0.125” Shaft Coupler over the turned side of the ¼-16 ACME Power Screw until the Shaft Coupler makes contact with the second Needle Thrust Bearing.

6. Tighten down all set screws. Apply Loctite to all threaded joints if connections feel loose or worn.
Motor Mount Sub-Assembly:
Part | QTY | Description
1 | 1 | BaneBots RS-550 Brushed DC Motor
2 | 1 | Motor Mounting Bracket
3 | 2 | M3 x 6mm Machine Screws

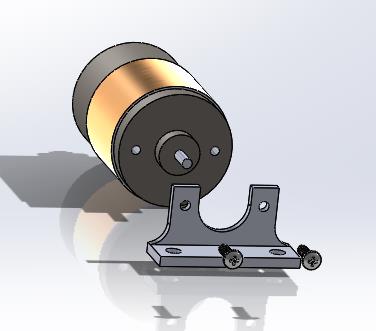
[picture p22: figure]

Instructions:
1. Align the metric 3 mounting holes on the BaneBots RS-550 DC motor with the mounting holes on the Motor Mounting Bracket.
2. Screw the Motor Mounting Bracket to the DC motor with the two M3 x 6mm Machine Screws.

Actuator Sub-Assembly:

Part | QTY | Description
1 | 1 | Motor Mount Sub-Assembly
2 | 1 | Power Train Sub-Assembly
3 | 2 | 10-32 x 5/8" Length Machine Screws
4 | 2 | 10-32 x 3/8" Length Machine Screws
5 | 1 | 7mm Precision Carriage
6 | 4 | M2 x 8mm Socket Headcap Screws
7 | 2 | 10-32 Nylon Lock Nuts
8 | 1 | Baseplate Sub-Assembly
9 | 1 | Sled Sub-Assembly

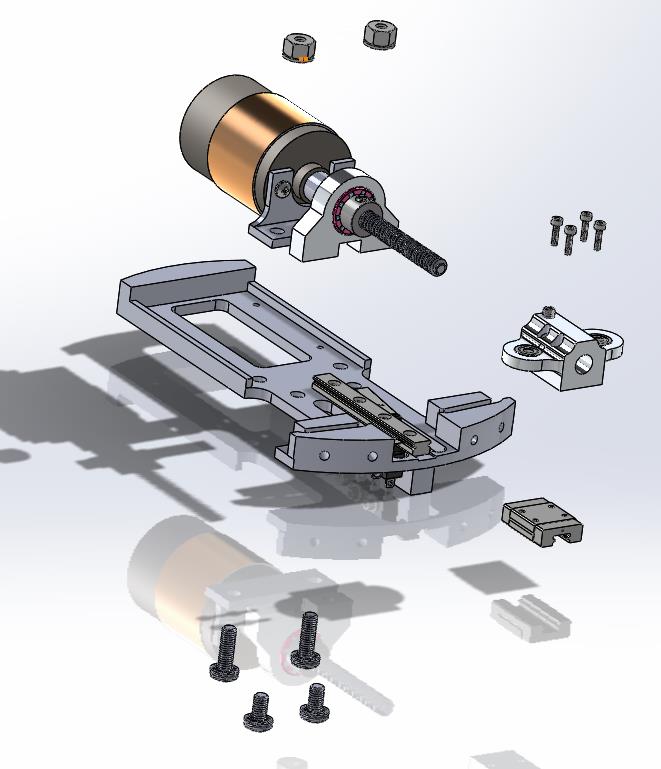
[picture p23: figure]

Instructions:
1. Screw the Sled Sub-Assembly onto the 7mm Precision Carriage (5) using the M2 x 8mm socket headcap screws (6).
2. Slide the motor shaft into the free side of the shaft coupler (located on the drive train sub-assembly).
3. align the 10-32 threaded mounting holes of both the motor mount and the journal with the 10-32 mounting holes on the baseplate.

4. Thread the ⅜” length 10-32 screws into the Journal. Leave them Hand tight for now.
5. Slide the ⅝” length 10-32 screws through the motor mount holes and thread the 10-32 nylon lock nuts over the top of the screws. Leave them hand tight for now.
6. Depress the lever of the front limit switch with a flathead screw driver or small allen key.
7. With the limit switch lever depressed, slide the sled and 7mm carriage assembly onto the 7mm precision rail. CAUTION: the limit switch can be easily damaged in this step. Additionally, the 7mm carriage contains dozens of 1/32” ball bearings in the bottom of it which can easily come out if the assembly is jarred. Take care in this step and be careful not to damage the components.
8. With the limit switch depressed and the sled assembly partially on the rail, hand turn the power screw until the entire sled assembly is on the rail and has cleared the front limit switch.
9. Tighten all screws and nuts using the appropriate tools. Tighten the set screws on the shaft coupler last. When tightening screws on the shaft coupler, rotate the power screw several times to ensure that the screw is aligned well and does not have any rough spots throughout its rotation.

Attaching the V-band to the Actuator Sub-Assembly:

Part | QTY | Description
1 | 1 | Actuator Sub-Assembly
2 | 2 | Dowel Pin Size 1
3 | 2 | Dowel Pin Size 2
4 | 8 | 1/8" E Clips
5 | 1 | V-Band
6 | 2 | 0.8” Relative Motion Arms

Instructions:
1. Attach one E Clip to the top side of each of the Size 2 Dowel Pins (the longer of the two).
2. Slide the front side (the front side has the shorter groove) of one of the relative motion arms over the connection tab of the V-band.
3. Slide one of the Size 2 Dowel Pins through the relative motion arm and V-band tab.
4. repeat steps 2 and 3 for the other relative motion arm and V-band tab.
5. Flip the V-band over and attach a second E Clip to the bottom of the dowel pin size 2.

6. Slide the V-band and relative motion arm assembly over the actuator sub-assembly. The exposed length of the dowel pins should seat into the guide rails of the baseplate.
7. Rotate the back side of the relative motion arms until the second set of holes lines up with the bearing holes in the sled.
8. Attach an E Clip to one side of each of the dowel pin size 1 pins.
9. Slide the pins through the relative motion arms and bearings.
10. Flip the assembly over and attach the last two E clips the the bottom side of the dowel pin size 1. Note: the bottom E Clips are very difficult to seat over the dowel pins and will test the patience of any mortal.

Male Coupling Ring and Wave Spring Sub-Assembly

Part | QTY | Description
1 | 3 | Indexing Tabs
2 | 1 | Male Coupling Ring
3 | 1 | Wave Spring (Smalley Springs SSR-0637)
4 | 3 | 4-40 x 0.25" Tapered Machine Screws

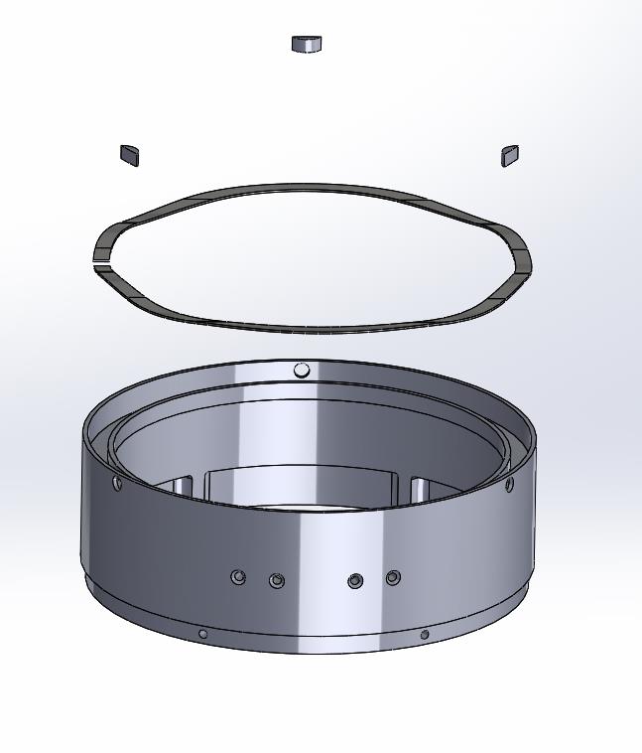
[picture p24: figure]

Instructions:
1. Place the wave spring in the groove of the male coupling ring.
2. Place the indexing tabs over the wave spring and line them up with the three holes in the side wall of the coupling ring.
3. Screw the 4-40 x 0.25” tapered machine screws into the side wall of the coupling ring. This will secure the wave spring into the provided groove.

Seating the Actuator and V-band Assembly into the Coupling Ring

The actuator and V-band assembly is fixed to the male coupling ring and wave spring assembly by seven 4-40 tapered machine screws. When seating the actuator assembly inside the male coupling ring assembly, gently thread all screws in until they are hand tight, alternating between the front four screws and back three screws. Gently tighten all screws down with an allen key only after all screws have been seated and are hand tight. Connect all electronics at this time. The actuator and male coupling ring assembly is now flight ready, and can be mated with the female coupling ring.

## Appendix G: Drawings

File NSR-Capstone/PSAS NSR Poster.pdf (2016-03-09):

Electro-Mechanical Nose Cone Separation Mechanism Miles Atherly, Benjamin Butler, Andrew Eads, Jason Hamilton, Brian Happ, Alin Resiga

Mechanical Engineering

# Problem Statement:

Most nose cone separation rings (NSR) use epoxy to secure the nosecone to the body of the rocket. Gunpowder deposited throughout the separation ring is ignited at apogee, separating the sections and deploying the parachute. Using epoxy to bind the rings is labor intensive, uses consumables, and is not easily testable. A more reliable method of binding and separating the rings is necessary on larger, more expensive rockets to ensure safe landing. The device needs to actuate quickly, be easily testable, and be able to withstand the forces experienced during rocket flight.

# Design Challenges:

The NSR is to be designed for use in Portland State Aerospace Societies LV3 launch vehicle. The LV3 is composed of modular sections that have an outer diameter of 6.6 inches and an inner diameter of 6 inches. The entire NSR device must fit within the nominal inner diameter of the LV3 rocket. The device needs to incorporate a kick-off mechanism, be able to withstand axial loadings of up to 250 lbf

, and have a verifiable failure rate of less than 1%.

# Results and Conclusions:

A working prototype of the separation mechanism was completed on time and under budget. A prototype control system was developed using an Arduino Uno R3, a 30 A H bridge, and a pair of limit switches. The device is capable of actuating in less than 63 milliseconds, can be easily reset, and is robust in design. The mechanical components of the NSR are rocket ready. However, a better control system should be developed and implemented prior to use on the LV3 launch vehicle.

# Detailed Design:

The electromechanical NSR design uses a Banebots RS-550 brushed DC motor to rotate a ¼-16 ACME power screw. The rotation of the power screw drives a rail guided sled assembly which interfaces with a V-band clamp through a set of relative motion arms. The motion of the arms are constrained by a set of pins which ride in a channel situated under the front of the sled. As the sled drives forward, tabs of the V-band are forced outward, increasing the diameter of the
band. | At | the | sleds | maximum
displacement, the V-band mates with a clamping surface on the rockets coupling rings. By reversing the current to the DC motor, the actuation is reversed. A wave spring incorporated in the larger coupling ring provides kick-off force, separating the two rings.


# Future Work:

The stall current of the selected motor is 85 A. The prototype control system currently in use limits the output current to 30 A. This does not allow the motor to be run at full power, and can cause the system to bind after repeated actuations or when the battery is low. The motor also spins up so quickly that the system exhibits measurable overshoot after crossing the limit switches. Both of these issues could be mitigated by developing a faster and more robust control system.


# Key Observations / Lessons Learned:

Figure 2: An exploded view of the NSR actuator


Figure 1: Solid model of the NSR

Finite Element Analysis (FEA) of the V-band showed that the maximum stress incurred by the band during actuation is 23.9 ksi. The yield strength for aluminum 6061-T6 is 40 ksi, yielding a factor of safety of 1.67. Fatigue analysis of the band suggests that the band will last through 44,000 actuation cycles. This exceeds the design requirements for mechanical failure 440 fold. Due to the tight spatial constraints, aligning all of the
mechanical | components | in | the
actuator proved to be extremely challenging. Custom dowel pins, shaft couplers, motor mounts and journals had to be made due to spatial constraints.


Figure 3: FEA of the V-band


Figure 4: Actuation path of sled and tabs

Figure 5: Completed electro-mechanical NSR

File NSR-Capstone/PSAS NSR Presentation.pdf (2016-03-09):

# PSAS Nosecone Separation Ring


Miles Atherly, Ben Butler, Andrew Eads,

### Jason Hamilton, Brian Happ, Alin Resiga

### Adviser: David Turcic

# Why This Project is Awesome

- One of only two entirely electro-mechanical NSR devices in existence (to
our knowledge)
- This will be the only electro-mechanical NSR device in use by an amatuer rocket club
- Significant challenges in both design and manufacturing
- Used many facets of engineering to complete the project

# Overview

# - Project Details

# - Design Challenges

# - Design Process

# - Prototyping

# - Manufacturing

# - Conclusions


# Nosecone Separation

### - Deploys parachute

### - Previous NSR used cyanoacrylate as an adhesive and gunpowder as the actuator - Very difficult to test for reliability

### - Failure destroys rocket

# Inspiration


Marmon Clamp | LightbandTM

# Design Challenges

- Entire device must fit inside 6” diameter ring
- Needs to be fast and be robust
- Torque / power requirements
- Isolation of components to avoid axial loading of motor

# Final Solid Model


# Analysis Based Design


- Used mathematical modeling, FEA, and real world testing on components under high stress loads
- Used statics, dynamics, vibrations, machine design and CAD software to assist in the design of moving parts and support structure

# V-Band Optimization


Model | Stress (psi) | Force Predicted (lbf)
Mathematical (Original) | NA | 18.2
Mathematical (Optimized) | NA | 15.68
Experimental | 37520 | 20.6
FEA (Original) | 36980 | 20.6
FEA (optimized) | 22866 | 16

# Design of Dynamic Action


- Model using rigid body kinematics
- End point (A) is equal to distance traveled by (B) plus rotation about part center

# Linear Motion Constraint


- Linear motion obtained using Guide rail and Power screw
- Guide rail assembly eliminates most friction and has 300 lbf dynamic load capacity
- Used needle thrust bearings to prevent transmission of axial load to motor

# Power Requirements


# Motor Selection


stall torque = 498 mNm

speed = 19300 RPM
(no load)

dimensions fit nominal for direct drive

total cost: $7.00 (does not include shipping and handling)

# Electrical System (Prototype)

- Motor controlled by PWM via Arduino
equipped with 30A H Bridge
- Push button operation (for display)


- Limit switches used as fore and aft stops
- Proprietary control board which interfaces with flight computer will be developed for use in LV3 vehicle

# How to Incorporate it All?

Limit Switch
Channels

Relative Motion
Guide Channels

Precision Rail
Slot and
Fixturing Holes


Motor and Journal
Mounting Holes

1.5” x 1.5” 4-40 UNF-2B
Mounting Hole Pattern
for Electronics

Motor Profile Relief
Cut

-.002/-.004
Diameter Control
Surface and
Mounting Holes

- All parts designed with ½” or ¼” tooling in mind (where allowable) for manufacturing


- Linear actuator parts must hold tight tolerancing to eliminate unwanted play. This was achieved by sizing and cutting the parts to each other
- Custom couplers and pins were manufactured due to space constraints

# Design Notes


# Prototyping: Coupling Rings


V-Band | Carriage


# Journal Arms

# Baseplate


# Machining

## V-Band


- Used 2-axis CNC to mill OD
- Turned 20deg clamping surface with custom tool
- Cut ID and relief cut with 2-axis

# Large and Small Rings


- Used Mastercam to define tool paths and write G code.
- Machined using 3-axis Haas mill
- Started with solid aluminum stock

## Challenges:

- 20 deg chamfer to interface with v-band
- 1/8” fillet
- Flipped part over several times

# Baseplate


- Machined on 3-axis Haas from 1/2” plate
- Significant challenges in fixturing
- 1/8” and .110” channels


# Fatigue

### - PDS Requirement: Mechanical failure of

less than 1%.

- 24 kpsi is maximum stress on the system.

### - Fatigue analysis shows V-band could be

actuated 44,000 times.

# Conclusions

- Mechanical components are rocket ready
- Design can withstand a 250 lbf tensile load required by PDS
- Actuates in ~63 milliseconds
- Needs more robust electrical system


# Questions?

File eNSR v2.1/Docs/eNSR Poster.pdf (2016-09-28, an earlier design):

Jorden Roland¹; , Katia Pahua Lopez; , David Edwards; , Adam Harris, Miles Atherly; , Benjamin Butler; , Andrew; Eads; , Jason Hamilton; , Brian Happ; , Alin Resiga; 1BS, Mechanical Engineering,; 2 BS, Physics; 3BS, Electrical Engineering; Amateur Rocket Recovery Systems

## PROBLEM/OPPORTUNITY

Figure 2: Detail of the original eNSR device.

## Electromechanical Nose Cone Separation Ring (eNSR) for Deployment of

The current industry standard nose cone release mechanism in amateur rocketry is a Pyrotechnically Initiated Release Mechanism (P.I.R.M.) which uses a combination of black powder and epoxy. Separation is achieved by detonating the black powder to release the nose cone.
The downfall of the pyrotechnic separation systems is that they cannot be tested without detonating the gunpowder charges, Making it difficult to predict if the system has been prepared correctly before launch. The epoxy commonly used to bind these types of separation rings together takes several hours to cure and can require several days of preparation to adequately assemble a working separation ring. Often rockets are at several kilometers up when the nosecone is released. This can be well out of view of operators on the ground. A system that provides feedback through the flight computer could give operators advanced warning of system failure.

MODEL, OBSERVATIONS,

## AND LEARNINGS

Figure 1: FEA analysis of the v-band clamp.

Portland State Aerospace society & The Beta Project

The final development of the first flight-ready eNSR is ongoing. Specifically, machining, integration, and testing. The team’s goal is to have it ready for launch in October 2016. This will be the first test launch of 3rd generation launch vehicle. The system must be reliable under the extreme stresses experienced in rocket flight while also being as light as safely possible. The system will undergo extensive testing under varying circumstances to simulate flight deployment conditions.

## RESULTS

Drawing inspiration from the $Lightband^{TM}$, a separation system designed by Planetary Systems and used in professional satellite deployment. The eNSR uses a single electric motor and a set of relative motion arms to translate the rotational motion of the motor into the linear motion required to actuate the clamping mechanism.
A flight weight version of the initial prototype was required in the LV3 rocket. To accomplish the required weight reduction a significant amount of material was removed from both the upper and lower rings to eliminate extraneous material that, in the prototype, had been left to streamline the manufacturing process.

## SPECIAL THANKS

Figure 3: Experimental verification of FEA

To understand the torque required to actuate the device, and to select an appropriate drive motor, several methods of analysis were employed.
The selected small brushless DC hobby motor, intended for use in quadcopters and model helicopters, provided the necessary speed and torque characteristics. These brushless DC motors are readily available in a wide range of specifications.

Specifically, cyclic loading test should tell us how many times it can be run before failure rate exceeds allowable limits. Actuation under simulated loads shows that the device will function under expected conditions. Simulated rocket flight, free fall off an airplane, tests device functionality in free fall conditions and compatibility with recovery systems deployment.

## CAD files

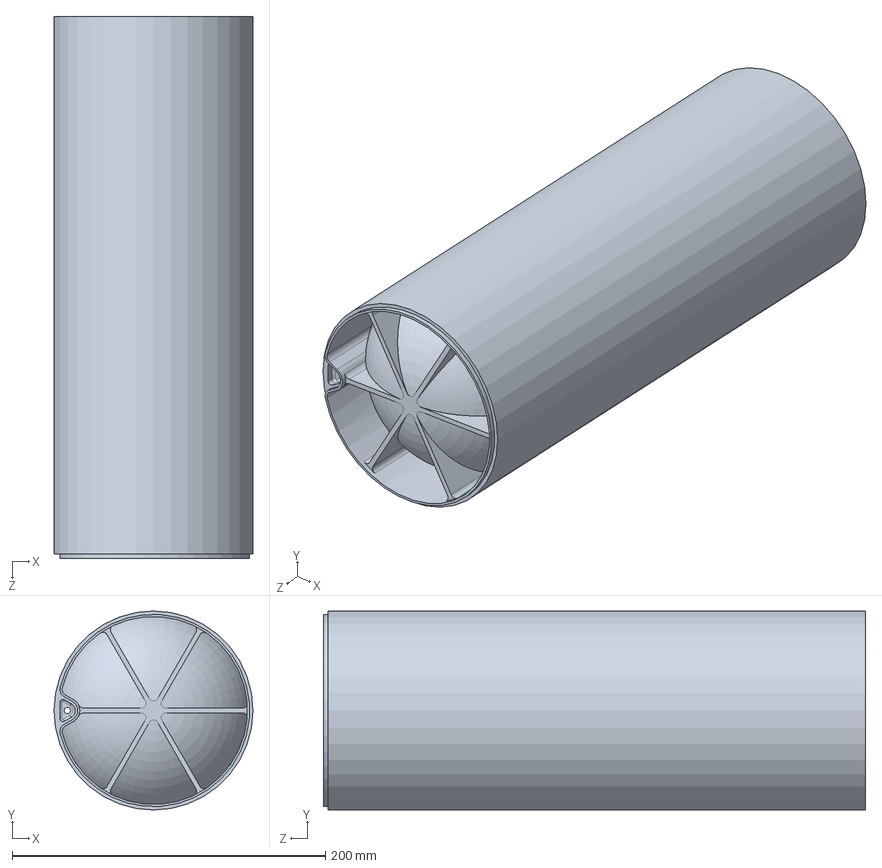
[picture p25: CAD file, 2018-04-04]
eNSR v2.2/Assemblies/Components/Cylinder_Chute_Main^eNSR_v2.2.sldprt
127.0 x 127.0 x 345.9 mm

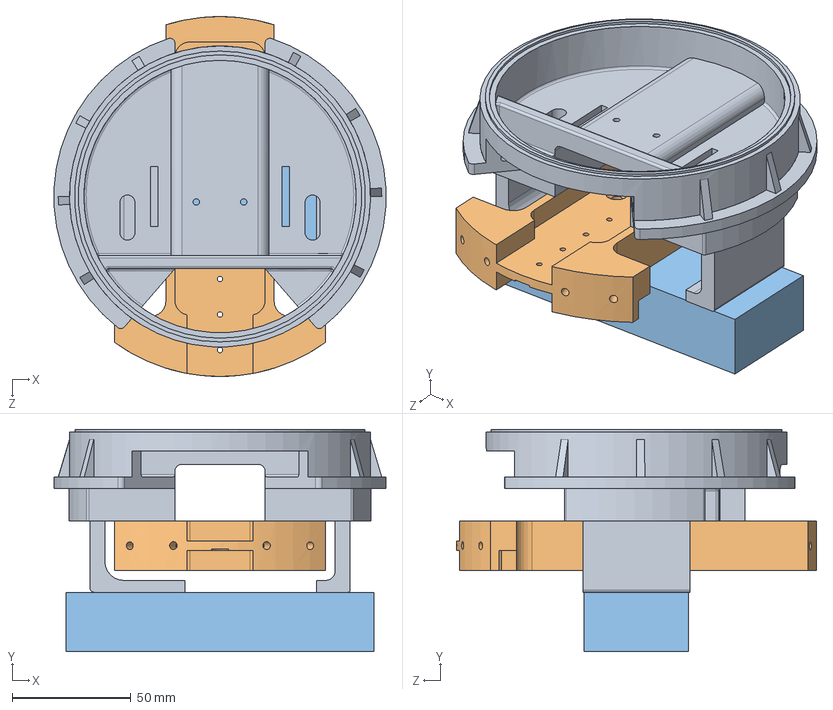
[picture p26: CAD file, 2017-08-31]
eNSR v2.2/Assemblies/ensr cap with vesc mount/ensr cap assembly.SLDASM
140.0 x 93.7 x 151.9 mm
eNSR_cap.2 with vesc mounting
Baseplate_v5
controller

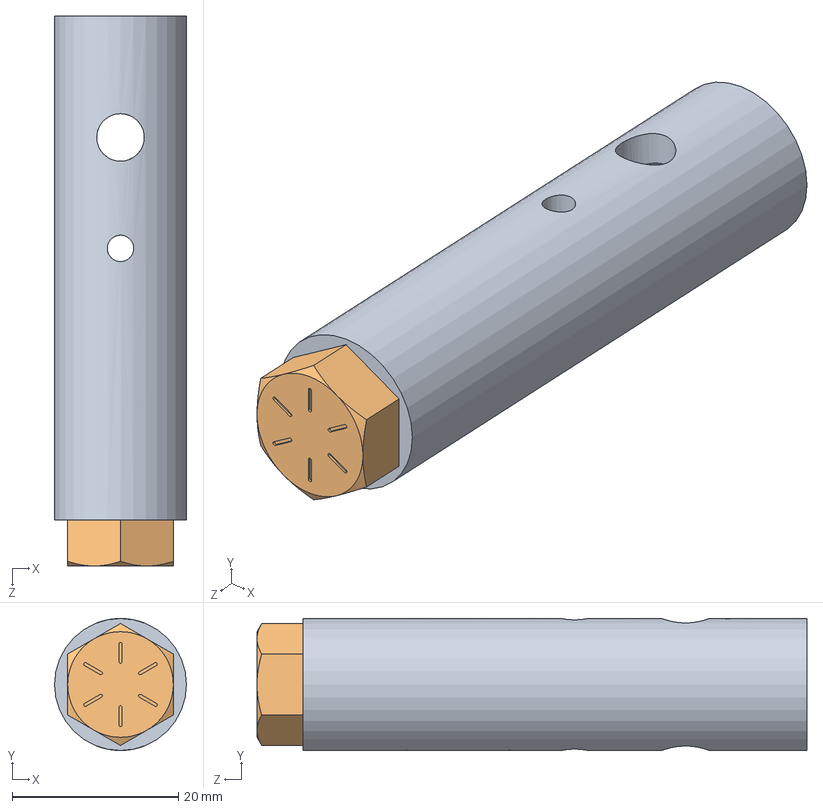
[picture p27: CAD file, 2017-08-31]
Line Cutters/Line Cutter Assembly.SLDASM
15.9 x 15.9 x 66.1 mm
LINE CUTTER TUBE
92620A605_HIGH-STRENGTH GRADE 8 STEEL CAP SCREW
Line Cutter Blade

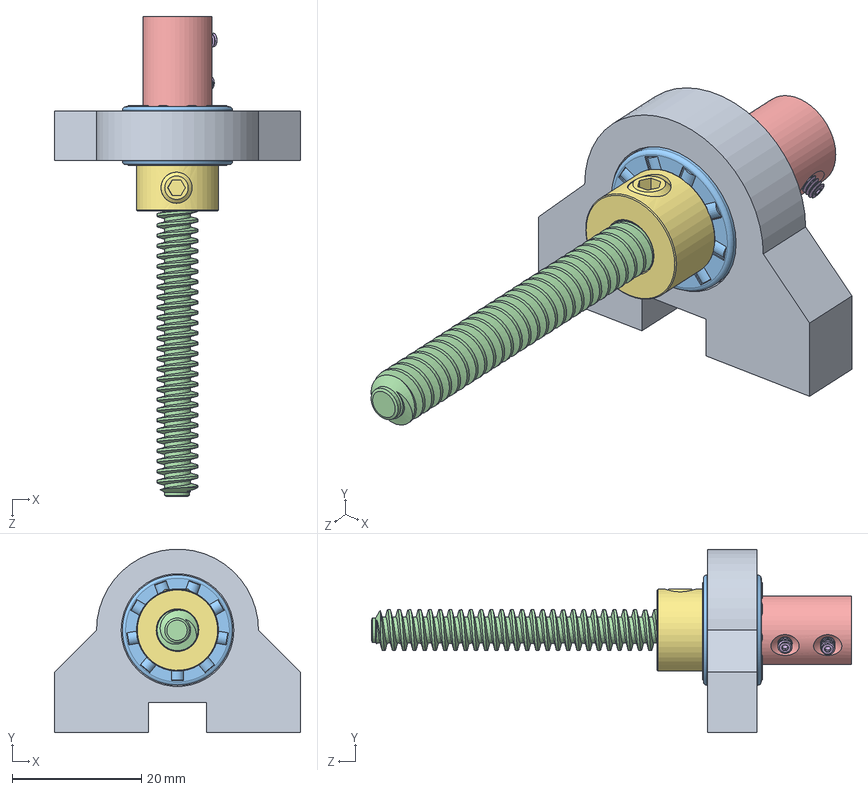
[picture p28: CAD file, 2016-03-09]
NSR-Capstone/Assembly models (breakout assembly)/power train assembly.SLDASM
38.1 x 28.4 x 74.3 mm
Journal_2
BearingAndWasher x 2
User Library-BEARING THRUST _25 ID _672 OD x 2
ACME_Screw
0.125_0.5_Coupler
97705A142 x 2
9414T600

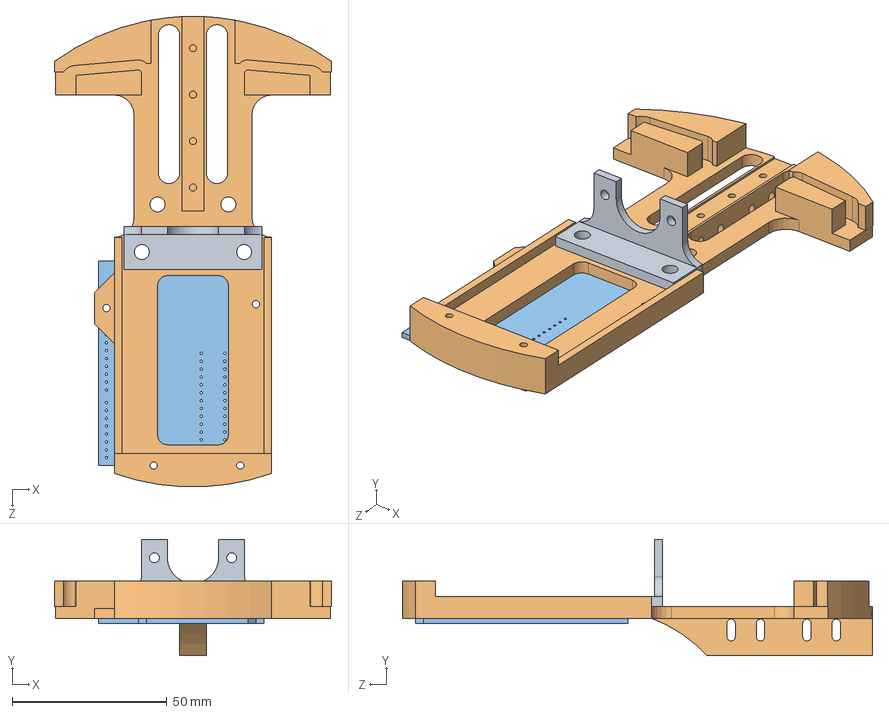
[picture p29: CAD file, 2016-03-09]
NSR-Capstone/carrige fea.SLDASM
89.4 x 37.6 x 151.8 mm
Motor Mount
Baseplate_3
unoboard blue

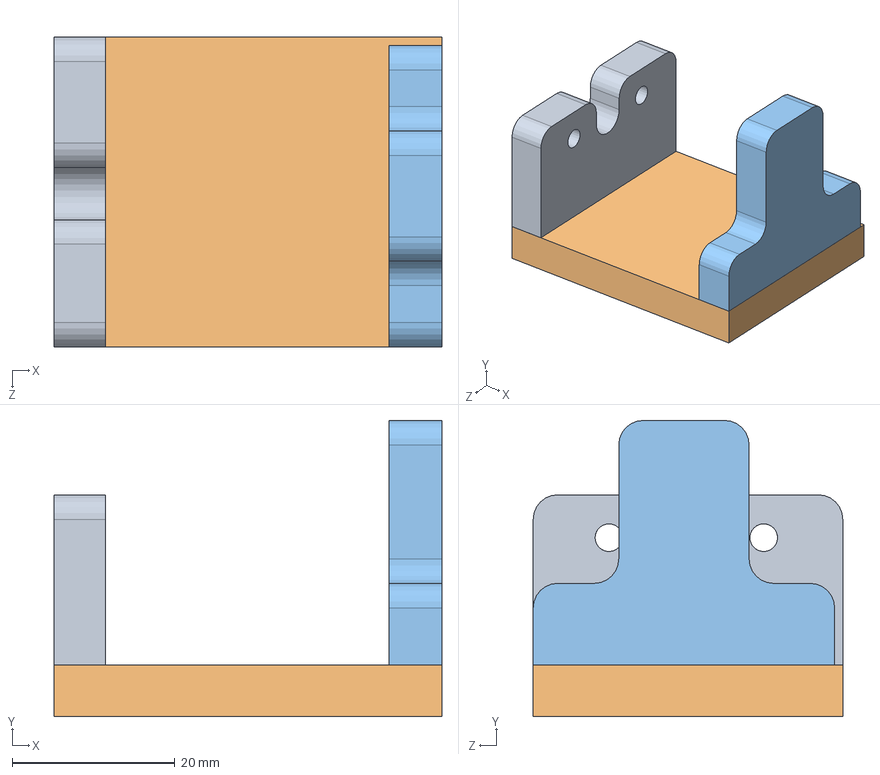
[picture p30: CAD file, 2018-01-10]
eNSR v2.2/eNSR Testing/eNSR_test_stand.SLDASM
47.6 x 36.3 x 38.0 mm
Bracket_Motor
bottom
sensor_bracket

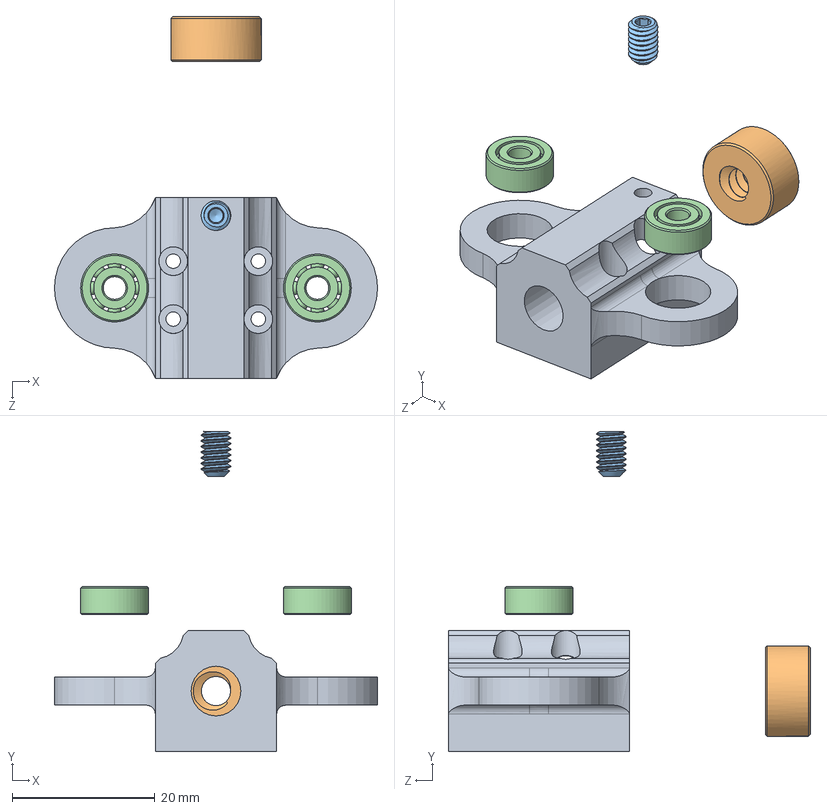
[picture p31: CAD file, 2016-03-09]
NSR-Capstone/Assembly models (breakout assembly)/carriage breakout.SLDASM
45.3 x 45.0 x 50.8 mm
Carriage_3
ACME threaded nut
97705A406
Bearing_RMA x 2

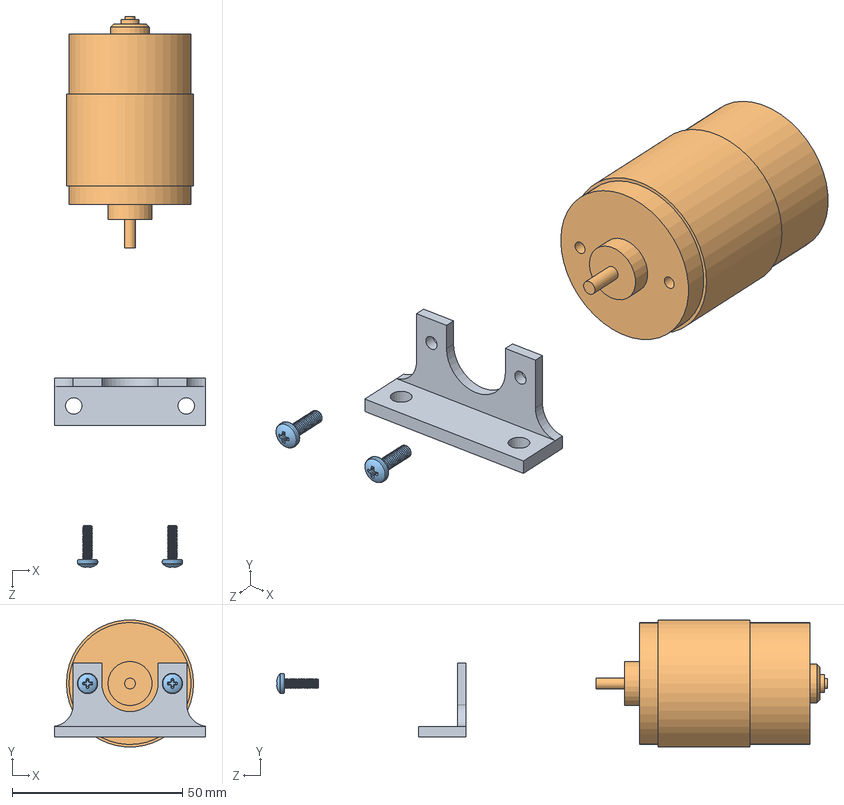
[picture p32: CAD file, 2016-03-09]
NSR-Capstone/Assembly models (breakout assembly)/motor mount.SLDASM
44.5 x 37.2 x 161.7 mm
Motor Mount
Motor1_small
92005A120 x 2

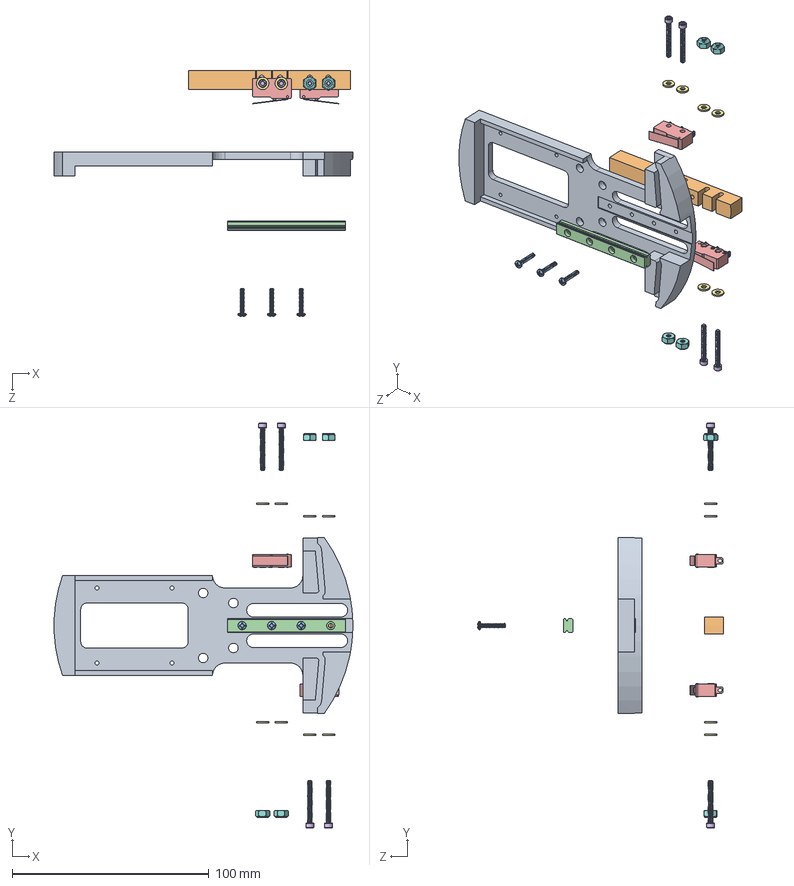
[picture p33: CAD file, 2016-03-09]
NSR-Capstone/Assembly models (breakout assembly)/base plate breakout.SLDASM
151.8 x 205.8 x 125.0 mm
Baseplate_4_MFG_coordinate
Mod_stem
91735A021 x 3
Rail
Micro Switch Button x 2
3-48_Screw x 4
#3Washer x 8
3-48_LockNut x 4

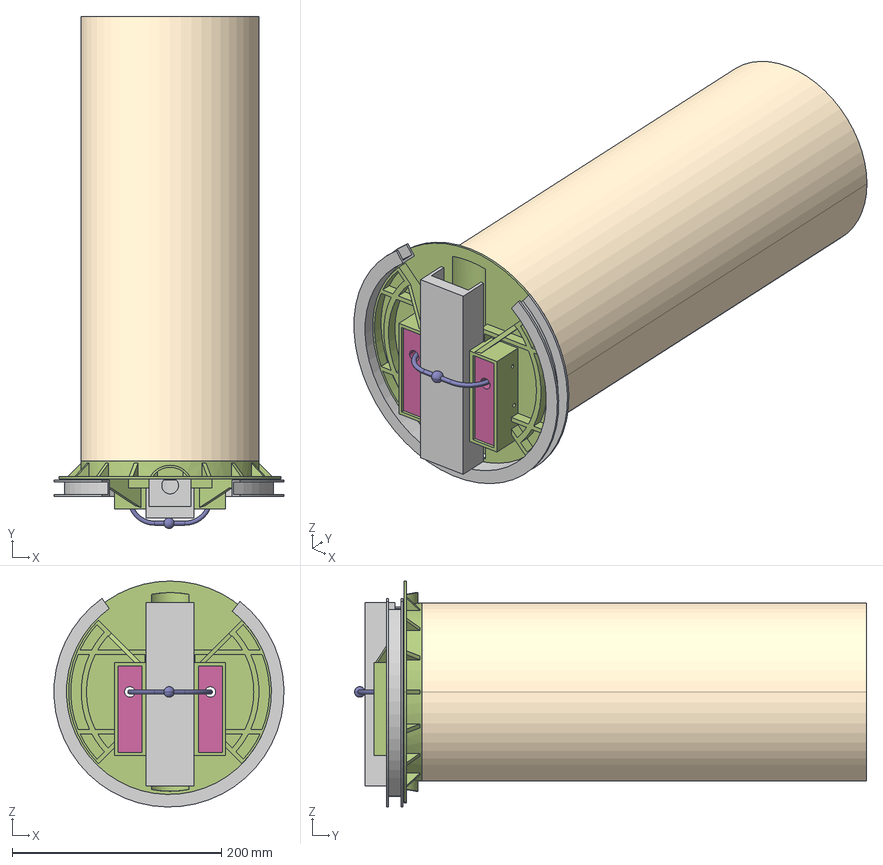
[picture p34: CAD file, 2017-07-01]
eNSR v2.2/CAD Sketches/ASSY-RECOVERY.stp
219.8 x 489.5 x 216.0 mm
CUT-LOOP
CAP
V-BAND
LINE-CUTTER x 2
MAIN-CYLINDER
BASEPLATE

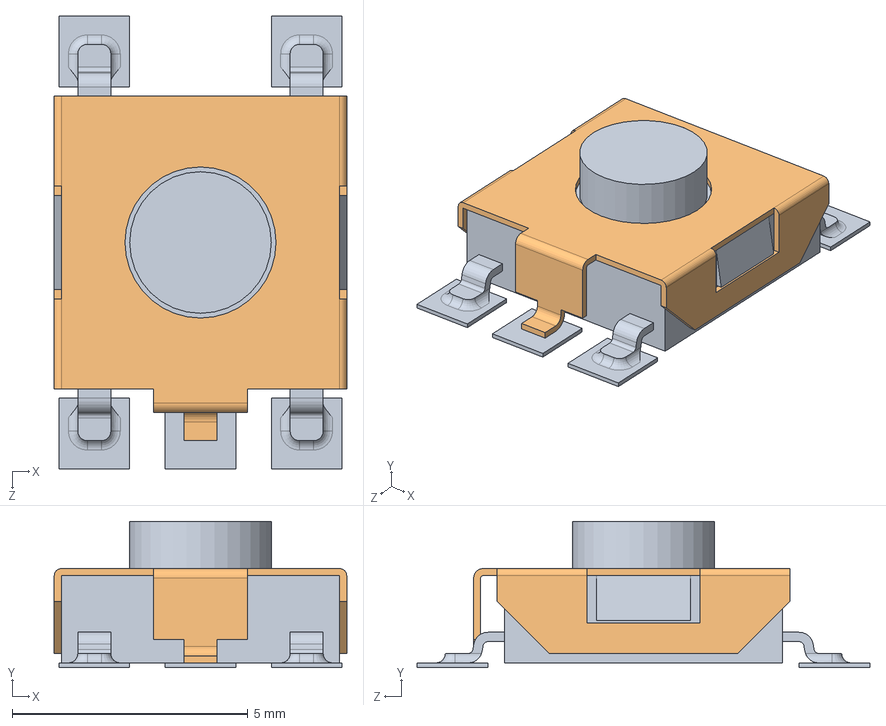
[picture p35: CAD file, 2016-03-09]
NSR-Capstone/Actuator Final/RESET BUTTON.SLDASM
6.20 x 3.10 x 9.60 mm
RESET CORE
RESET

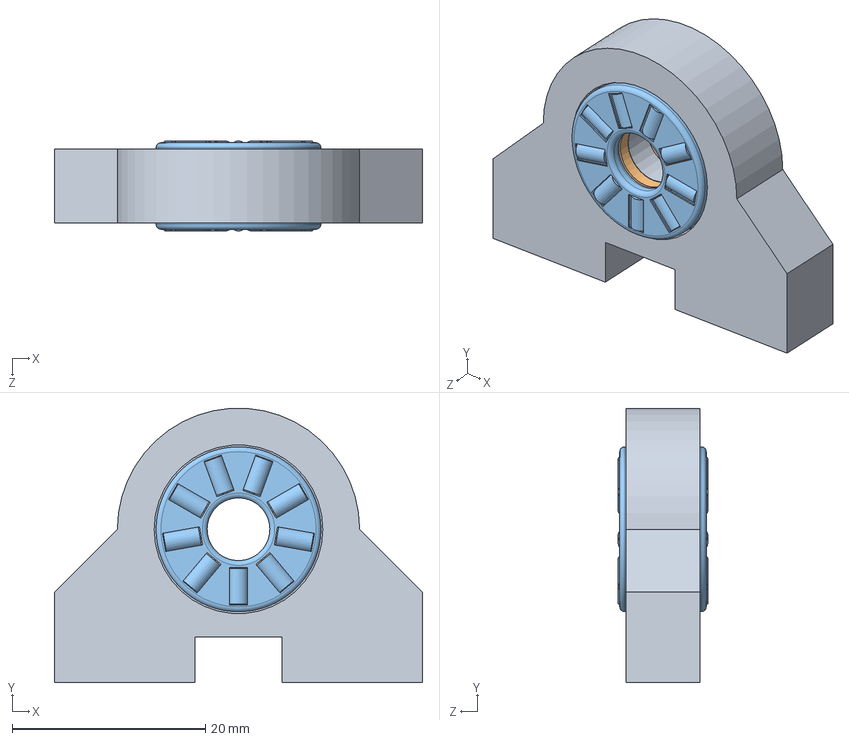
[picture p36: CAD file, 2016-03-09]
NSR-Capstone/Actuator Complete/Journal-bearing-sub.SLDASM
38.1 x 28.4 x 9.31 mm
Journal_2
BearingAndWasher x 2
User Library-BEARING THRUST _25 ID _672 OD x 2

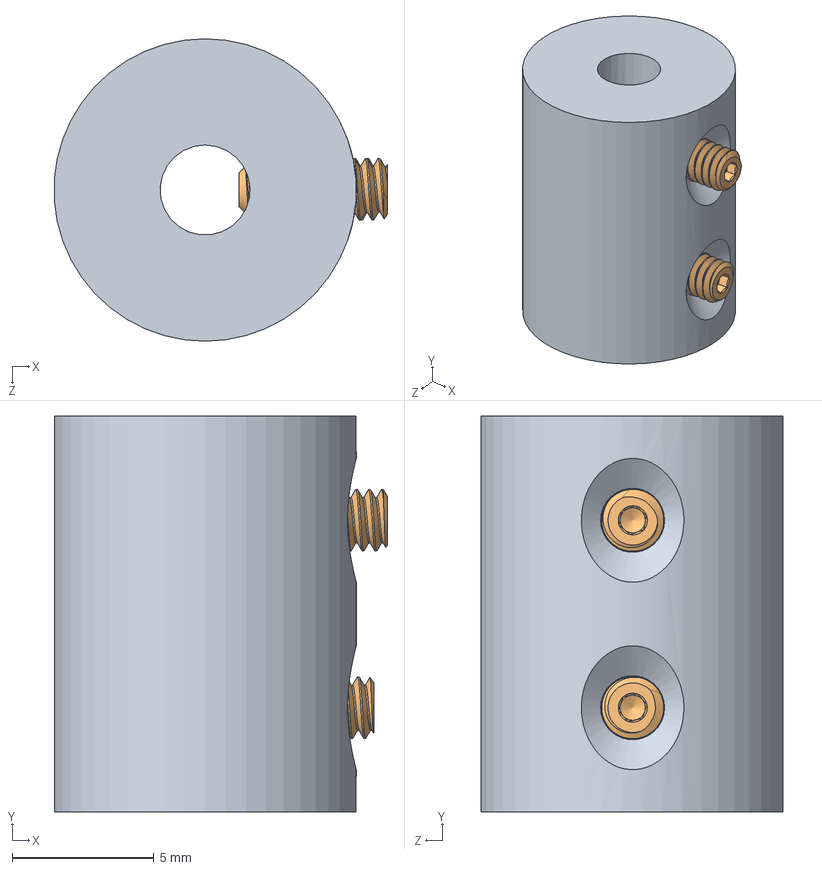
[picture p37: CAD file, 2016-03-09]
NSR-Capstone/Actuator Complete/0.125_0.5_Coupler.SLDASM
11.8 x 14.0 x 10.7 mm
0.125_0.5_Coupler
97705A142 x 2

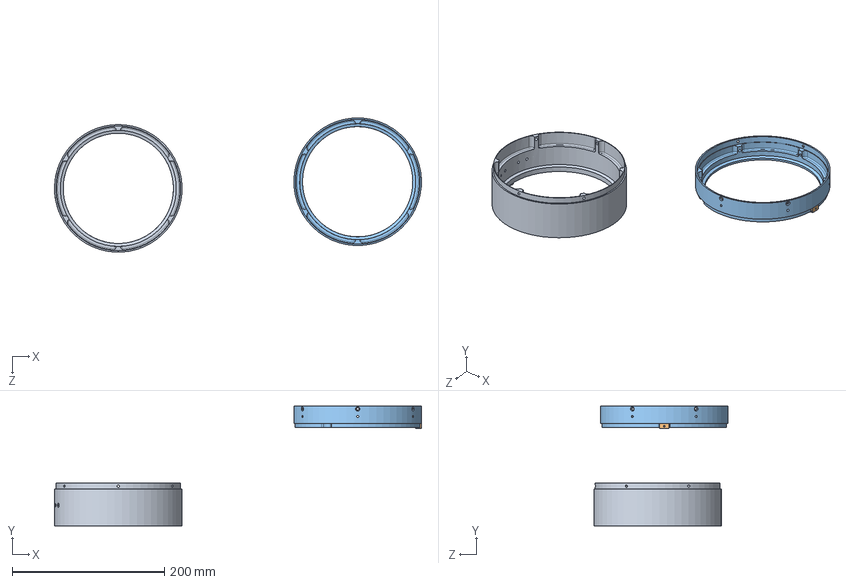
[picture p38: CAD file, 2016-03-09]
NSR-Capstone/Actuator Complete/test fit tabs.SLDASM
481.9 x 157.4 x 176.3 mm
NSR_CR_F_3_FINAL_FINAL_corrected
Male index tabs x 2
NSR_CR_M2_final_final_w_coordinate2

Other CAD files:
eNSR v2.2/CAD Sketches/MAIN-CYLINDER.sldprt
NSR-Capstone/Actuator Final/0.125_0.5_Coupler.SLDASM
NSR-Capstone/Actuator Final/USB type b.SLDPRT.SLDASM
NSR-Capstone/Actuator Final/arduino uno.SLDASM
LV2.3_NSR/NSR_Bottom.SLDPRT
LV2.3_NSR/NSR_Top.SLDPRT
Line Cutters/92620A605_HIGH-STRENGTH GRADE 8 STEEL CAP SCREW.SLDPRT
Line Cutters/LINE CUTTER TUBE.SLDPRT
Line Cutters/Line Cutter Blade.SLDPRT
NSR-Capstone/Actuator Complete/#3ScrewAndNut.SLDASM
NSR-Capstone/Actuator Complete/#3Washer.SLDPRT
NSR-Capstone/Actuator Complete/0.125_0.5_Coupler.SLDPRT
NSR-Capstone/Actuator Complete/3-48_LockNut.SLDPRT
NSR-Capstone/Actuator Complete/3-48_Screw.SLDPRT
NSR-Capstone/Actuator Complete/91290A015.SLDPRT
NSR-Capstone/Actuator Complete/91735A021.SLDPRT
NSR-Capstone/Actuator Complete/9414T600.SLDPRT
NSR-Capstone/Actuator Complete/95345A091.SLDPRT
NSR-Capstone/Actuator Complete/97705A142.SLDPRT
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

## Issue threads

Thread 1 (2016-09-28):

Machining eNSR parts

JSRoland, 2016-09-28:
The following parts need to be machined to have a complete recovery system. If you have some free time and/or want some experience in the machine shop grab a drawing and go make a thing.

- [ ] Baseplate

- [ ] Carriage

- [ ] Dowel pins 1 & 2

- [ ] Motor mount

- [ ] RMA (x2)

- [ ] V-band

JacobTiller, 2016-11-30:
I recently got machine shop access and want to start working on some simple parts.  Do you already have the needed metal for making the parts?  The motor mount says 'made from provided angle stock'.

Also, it looks like a few of the drawings are missing the material call outs.  Are the dowels T6061 Al?

7deeptide, 2017-02-02:
@JSRoland Jorden, have any of these issues been closed?

JSRoland, 2017-02-02:
The upper ring exists assuming Calvin found it otherwise I don't believe so.

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

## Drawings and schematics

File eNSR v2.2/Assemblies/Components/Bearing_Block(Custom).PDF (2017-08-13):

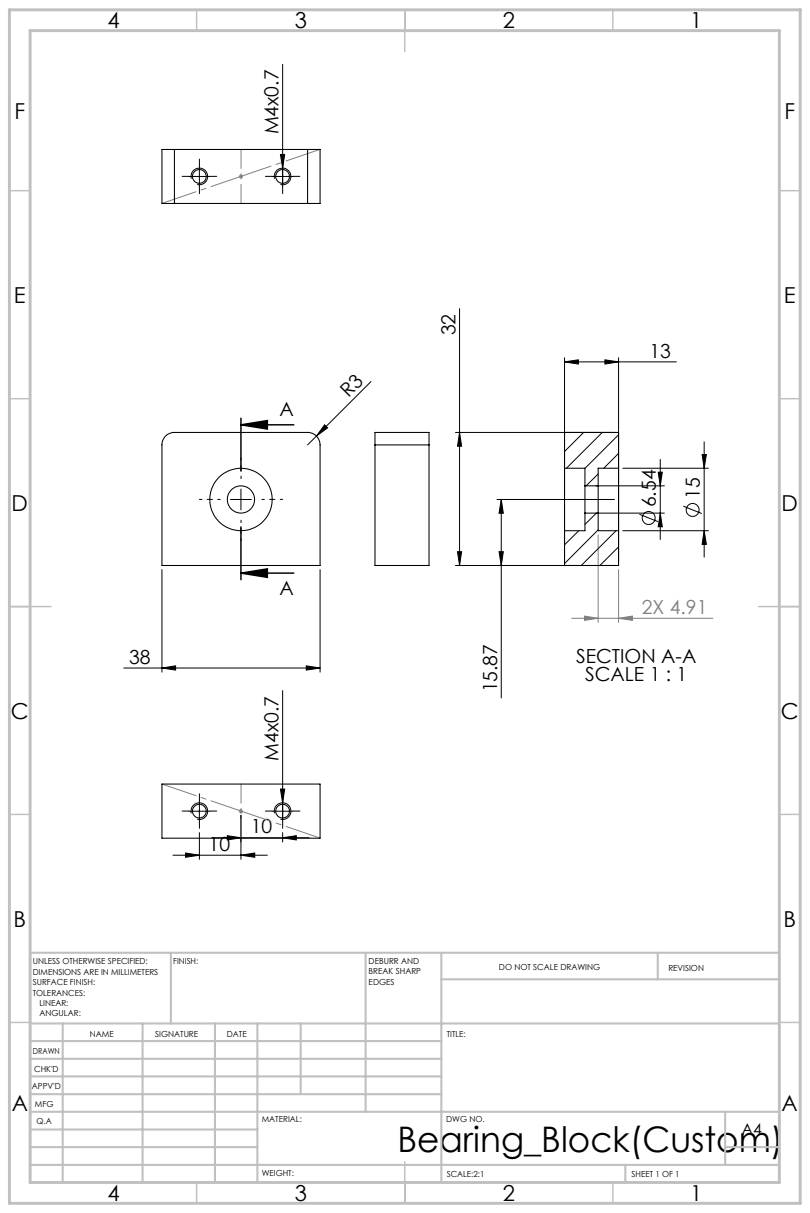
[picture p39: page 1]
SECTION A-A SCALE 1 : 1; FINISH:; DEBURR AND; BREAK SHARP; DO NOT SCALE DRAWING; REVISION; SCALE:2:1; SHEET 1 OF 1

UNLESS OTHERWISE SPECIFIED:
DIMENSIONS ARE IN MILLIMETERS
SURFACE FINISH:
TOLERANCES:
LINEAR:
ANGULAR:

NAME | SIGNATURE | DATE | | | | TITLE:

DRAWN
CHK'D
APPV'D
MFG
Q.A | | | | MATERIAL: Bearing_Block(Custom) | DWG NO. | A4

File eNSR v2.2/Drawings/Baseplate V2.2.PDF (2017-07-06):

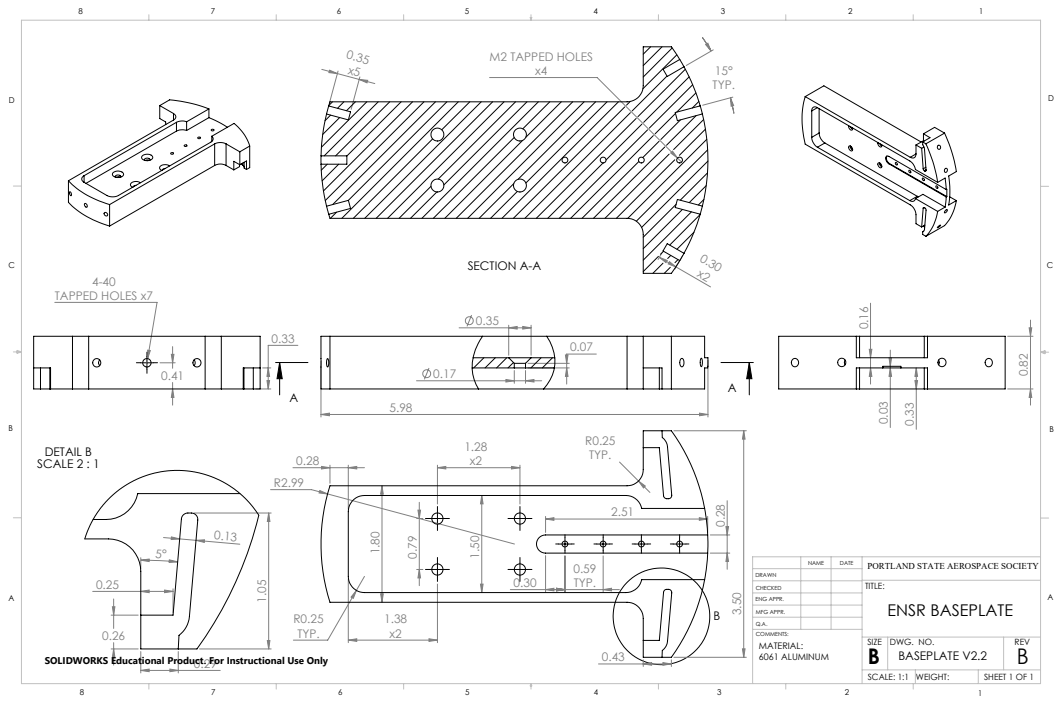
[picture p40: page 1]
TAPPED HOLES x7; M2 TAPPED HOLES; SECTION A-A; DETAIL B SCALE 2 : 1; BASEPLATE V2.2; ENSR BASEPLATE; 6061 ALUMINUM; ENG APPR.; MFG APPR.; NAME; DATE; PORTLAND STATE AEROSPACE SOCIETY; DWG. NO.; REV; SCALE: 1:1 WEIGHT:; SHEET 1 OF 1

SOLIDWORKS Educational Product. For Instructional Use Only

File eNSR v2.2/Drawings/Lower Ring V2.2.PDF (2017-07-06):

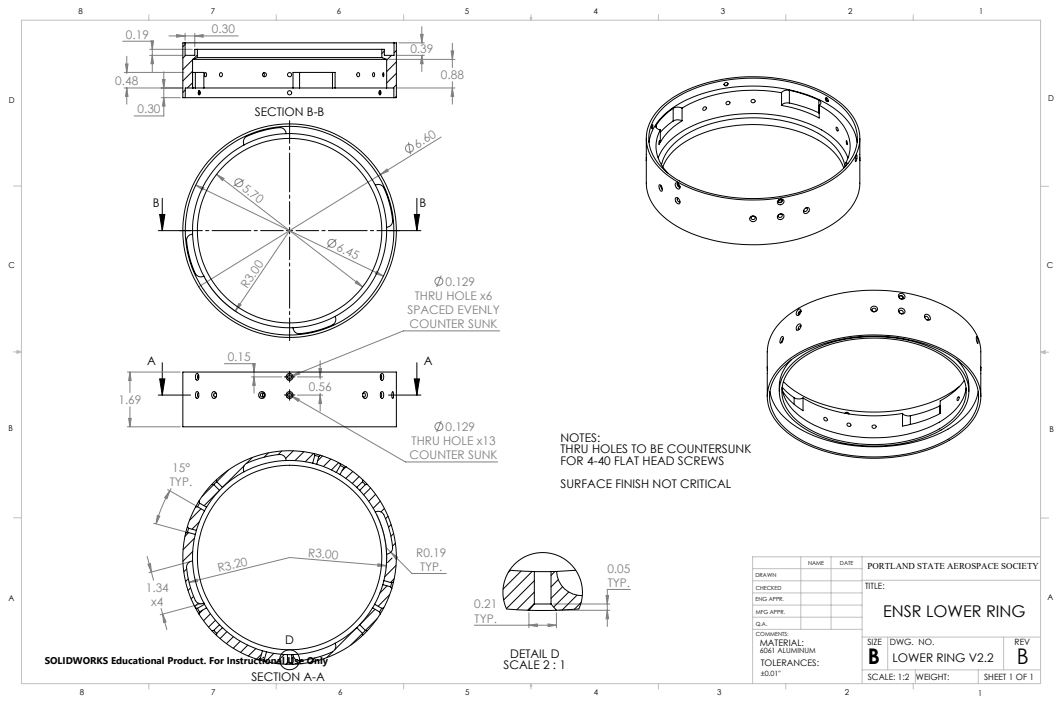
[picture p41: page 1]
THRU HOLE x6 SPACED EVENLY COUNTER SUNK; THRU HOLE x13 COUNTER SUNK; SECTION A-A; SECTION B-B; DETAIL D; SCALE 2 : 1; LOWER RING V2.2; ENSR LOWER RING; 6061 ALUMINUM; ENG APPR.; MFG APPR.; NAME; DATE; PORTLAND STATE AEROSPACE SOCIETY; DWG. NO.; REV; SCALE: 1:2 WEIGHT:; SHEET 1 OF 1

NOTES:
THRU HOLES TO BE COUNTERSUNK
FOR 4-40 FLAT HEAD SCREWS
SURFACE FINISH NOT CRITICAL

SOLIDWORKS Educational Product. For Instructional Use Only

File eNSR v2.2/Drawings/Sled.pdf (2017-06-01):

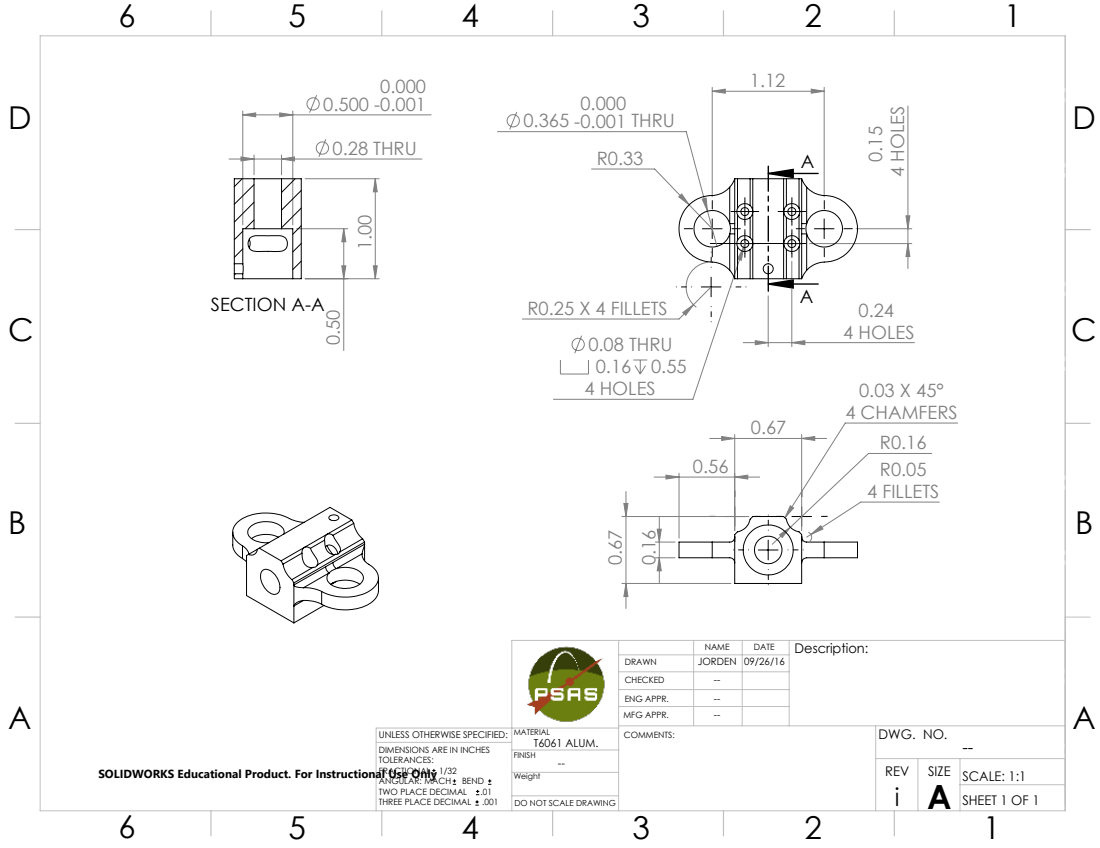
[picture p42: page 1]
4 FILLETS; 0.03 X 45° 4 CHAMFERS; 0.365 - 0.001 THRU; R0.25 X 4 FILLETS 0.08 THRU 0.16 0.55 4 HOLES; 4 HOLES; 0.28 THRU; SECTION A-A; REV; SCALE: 1:1; DO NOT SCALE DRAWING; SHEET 1 OF 1

NAME | DATE | Description:

DRAWN | JORDEN | 09/26/16
CHECKED | --
ENG APPR. | --
MFG APPR. | --

UNLESS OTHERWISE SPECIFIED: | MATERIAL T6061 ALUM. | COMMENTS: | DWG. NO. --

DIMENSIONS ARE IN INCHES
TOLERANCES:
FRACTIONAL 1/32
ANGULAR: MACH BEND
TWO PLACE DECIMAL .01
THREE PLACE DECIMAL .001

SOLIDWORKS Educational Product. For Instructional Use Only

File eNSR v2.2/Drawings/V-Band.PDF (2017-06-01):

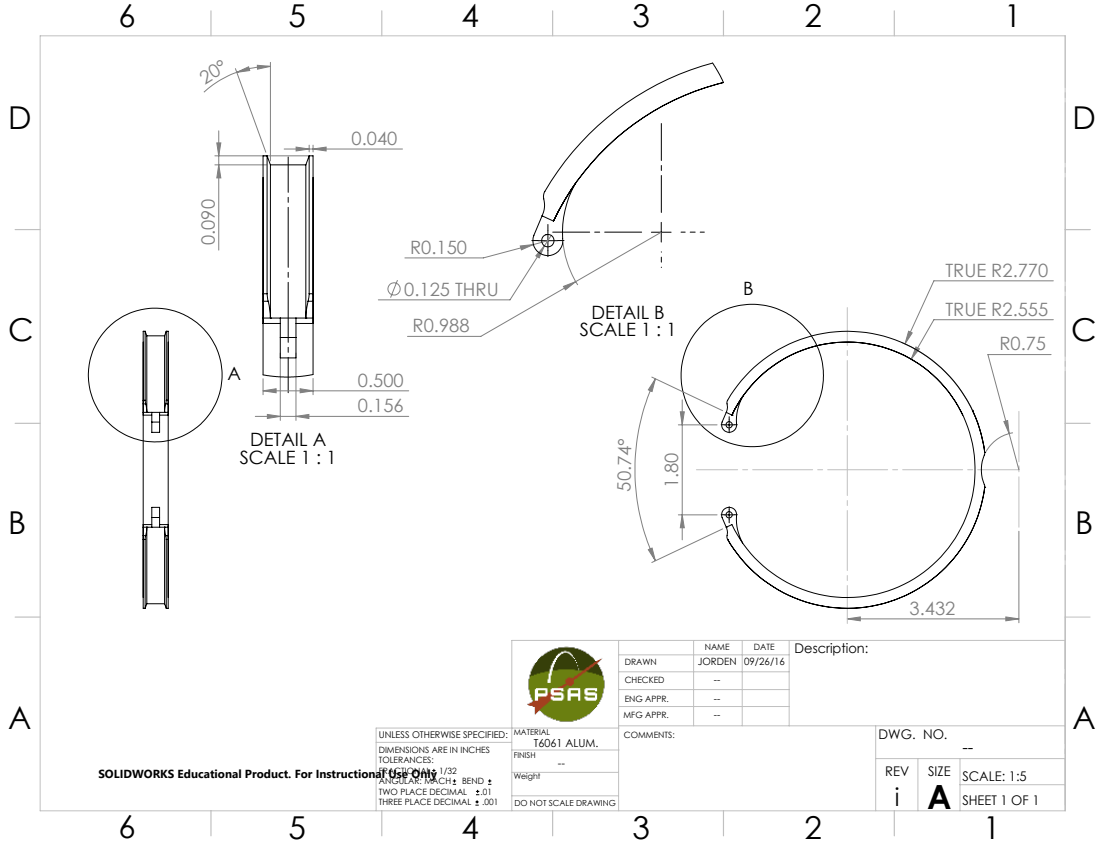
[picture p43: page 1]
TRUE R2.555; TRUE R2.770; 0.125 THRU; DETAIL B SCALE 1 : 1; DETAIL A SCALE 1 : 1; REV; SCALE: 1:5; DO NOT SCALE DRAWING; SHEET 1 OF 1

NAME | DATE | Description:

DRAWN | JORDEN | 09/26/16
CHECKED | --
ENG APPR. | --
MFG APPR. | --

UNLESS OTHERWISE SPECIFIED: | MATERIAL T6061 ALUM. | COMMENTS: | DWG. NO. --

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

SOLIDWORKS Educational Product. For Instructional Use Only

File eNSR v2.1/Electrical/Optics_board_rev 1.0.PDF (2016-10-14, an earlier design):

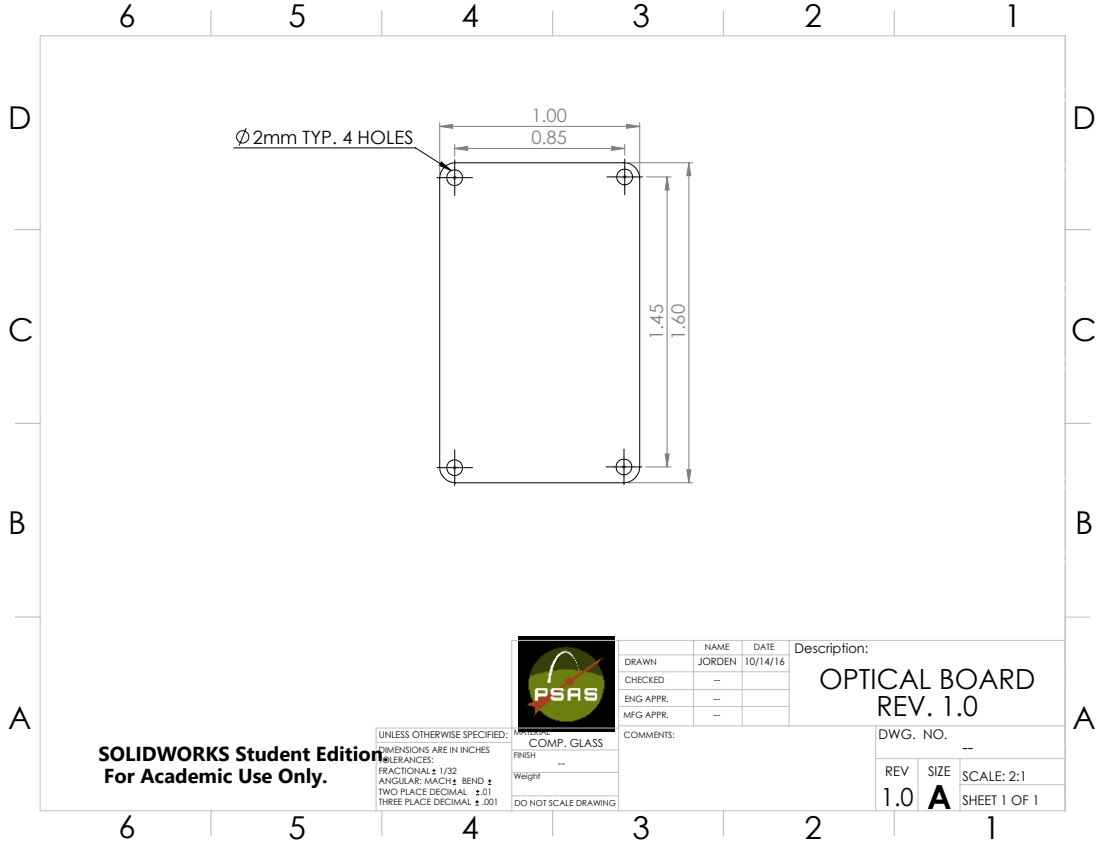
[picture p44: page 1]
2mm TYP. 4 HOLES; REV; SCALE: 2:1; DO NOT SCALE DRAWING; SHEET 1 OF 1

NAME | DATE | Description: OPTICAL BOARD REV. 1.0

DRAWN | JORDEN | 10/14/16
CHECKED | --
ENG APPR. | --
MFG APPR. | --

UNLESS OTHERWISE SPECIFIED: | MATERIAL COMP. GLASS | COMMENTS: | DWG. NO. -- SOLIDWORKS Student Edition.

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

For Academic Use Only.

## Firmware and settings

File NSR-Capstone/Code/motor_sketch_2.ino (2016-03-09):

//NSR motor control sketch
//5-26-2015
//Miles Atherly
//Use 11.1V 3000 mAh Lectron Pro LiPo battery and ___ motor

/* The motor variable in each function should be either a 0 or a 1.
 pwm in the motorGo function should be a value between 0 and 1023.
*/
 
#define BRAKEVCC 0
#define CW   1
#define CCW  2
#define BRAKEGND 3
#define CS_THRESHOLD 100

/*  VNH2SP30 pin definitions
 xxx[0] controls '1' outputs
 xxx[1] controls '2' outputs */

int inApin[2] = {7, 4};  // INA: Clockwise input
int inBpin[2] = {8, 9}; // INB: Counter-clockwise input
int pwmpin[2] = {5, 6}; // PWM input
int cspin[2] = {2, 3}; // CS: Current sense ANALOG input
int enpin[2] = {0, 1}; // EN: Status of switches output (Analog pin)

int BUTTON = A2; //button input pin

int ls1=11; //limit switch 1 input pin
int ls2=12; //limit switch 2 input pin


int buttonstate=0;
int ls1state=0;
int ls2state=0;


void setup() {
 Serial.begin(9600);
  
  pinMode(BUTTON, INPUT_PULLUP);  //declare input pin for button
  pinMode(ls1, INPUT_PULLUP); //declare input pin for limit switch 1
  pinMode(ls2, INPUT_PULLUP); //declare input pin for limit switch 2
  

  // Initialize digital pins as outputs
  for (int i=0; i<2; i++)
  {
    pinMode(inApin[i], OUTPUT);
    pinMode(inBpin[i], OUTPUT);
    pinMode(pwmpin[i], OUTPUT);
  }
  // Initialize braked
  for (int i=0; i<2; i++)
  {
    digitalWrite(inApin[i], LOW);
    digitalWrite(inBpin[i], LOW);
  }
   //motorGo(0, CW, 1023);
  // motorGo(1, CCW, 1023);
}


void loop() {
  buttonstate=digitalRead(BUTTON);
  ls1state=digitalRead(ls1);
  ls2state=digitalRead(ls2);
  //Serial.print("read switch input: ");
  //Serial.print(digitalRead(BUTTON));
  //Serial.print(", ");
  //Serial.print(digitalRead(ls1));
  //Serial.print(", ");
  //Serial.println(digitalRead(ls2));
  //delay(100);
  
  if(BUTTON == HIGH && ls1 == HIGH){
    motorGo(1, CW, 500);
    if(ls2 == HIGH){
      motorGo(1, CW, 0);
    }
  }
  else if(BUTTON == HIGH && ls2 == HIGH){
    motorGo(1, CCW, 500);
    if(ls1 == HIGH){
      motorGo(1, CCW, 0);
    }
  }
}


void motorOff(int motor)
{
  // Initialize braked
  for (int i=0; i<2; i++)
  {
    digitalWrite(inApin[i], LOW);
    // digitalWrite(inBpin[i], LOW);
  }
  analogWrite(pwmpin[motor], 0);
}


void motorGo(uint8_t motor, uint8_t direct, uint8_t pwm)
{
  if (motor <= 1)
  {
    if (direct <=4)
    {
      // Set inA[motor]
      if (direct <=1)
        digitalWrite(inApin[motor], HIGH);
      else
        digitalWrite(inApin[motor], LOW);

      // Set inB[motor]  
      if ((direct==0)||(direct==2))
        digitalWrite(inBpin[motor], HIGH);
      else
        digitalWrite(inBpin[motor], LOW);

      analogWrite(pwmpin[motor], pwm);
    }
  }
}

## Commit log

2014-08-01 Initial move of CAD files to git out of dropbox
    [NSR_Bottom.SLDPRT, NSR_Top.SLDPRT]
2015-06-17 Adding CAD data from Miles during capstone hand off meeting
    [#3ScrewAndNut.SLDASM, #3Washer.SLDPRT, 0.125_0.575_Coupler.SLDDRW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]
2016-02-09 Initial commit of the eNSR v2.0
    Updated rings
    [Baseplate_3.SLDPRT, Baseplate_3.STL, Motor Mount.SLDPRT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]
2016-03-03 created Dyno file
    [NSRlower 2.0v1.SLDPRT, NSRupperv2.0.SLDPRT]
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2016-03-09 fixed the broken Dyno folder
    [Dyno base plate.SLDPRT, Dyno_assem.SLDASM, Dyno_generator.SLDPRT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]
2016-03-09 Mass update of fixed files.
    [Dyno base plate.SLDPRT, Dyno_assem.SLDASM, Dyno_generator.SLDPRT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]
2016-03-09 still oops
    [Dyno base plate.SLDPRT, Dyno_assem.SLDASM, Dyno_generator.SLDPRT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]
2016-03-09 fix oopsies again maybe
    [Dyno base plate.SLDPRT, Dyno_assem.SLDASM, Dyno_generator.SLDPRT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]
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2016-03-10 raw data dump of initial motor tests using dyno
    [LJLogUD.cfg]
2016-03-11 mostly complete Dyno assembly model
    [Dyno_assem.SLDASM, Large_motor_mount_dyno.SLDPRT]
2016-04-07 Major redesign of lower ring concept.
    [LJLogUD_open.cfg, NSRlower 2.0v2 concept.SLDPRT, NSRupperv2.0.SLDPRT]
2016-05-17 lots of CAD work
    [91290A015.SLDPRT, 91735A021.SLDPRT, 91735A102.SLDPRT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]
2016-05-18 Drawings for machining various parts added
    [ACME_Screw_SY_set.SLDDRW, motor mount.SLDDRW, motor mount.SLDPRT]
2016-09-16 Organized assemblies and removed duplicate parts.
    [91290A015.SLDPRT, 91735A021.SLDPRT, 91735A102.SLDPRT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]
2016-09-28 add drawings.
    [Baseplate.SLDDRW, Carriage.SLDDRW, NSR lower ring.SLDDRW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]
2016-10-14 added board outline for optical sensors.
    [Optics_board.SLDPRT, Optics_board_rev 1.0.SLDDRW]
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2016-10-14 try again.
    [Optics_board_rev 1.0.SLDDRW]
2017-05-14 Fixed full assembly, added nosecone and femalering
    [Complete final.SLDASM, Spring_Ring_r61.SLDPRT, nosecone_forstone.SLDPRT]
2017-05-15 updated lower ring with just in case holes
    [NSRlower 2.0v5 flipped.SLDPRT]
2017-05-21 Re-organized the directories a little bit
    [91290A015.SLDPRT, 91735A021.SLDPRT, 91735A102.SLDPRT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]
2017-05-22 Improved mates within assembly
    [complete.SLDASM, cylinder.SLDPRT]
2017-05-22 Working on making the assembly more perfect; added some recovery hardware
    [ACME threaded nut.SLDPRT, Baseplate_v4.SLDPRT, Bearing_RMA.SLDPRT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]
2017-05-27 Renamed some bullshit
    [Carriage_3.SLDPRT, RMA.sldasm, Rail.SLDPRT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]
2017-05-27 Oops accidentally deleted some things
    [Carriage(6725K2).SLDPRT, Rail(6725K33).SLDPRT, Sled(Custom).SLDPRT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]
2017-05-28 Completed assembly - added fasteners, fixed mates - ready for review by Jorden
    [91290A015.SLDPRT, 91735A021.SLDPRT, 91735A102.SLDPRT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]
2017-06-01 Updated some drawings, made PDFs for them
    [Carriage.SLDDRW, Sled.SLDDRW, V-Band.SLDDRW]
2017-06-04 Edited the ensr to accomodate thicker baseplate, extended ring, edited motor mount
    [Baseplate_v5.SLDPRT, Fasteners.sldasm, Journal_2.SLDPRT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]
2017-06-09 readded wave spring recess that was accidentally deleted
    [NSRlower 2.0v5.SLDPRT]
2017-06-16 Fixed the sled...
    [Sled(Custom).SLDPRT]
2017-06-16 Removed sensor holes in baseplate
    [Baseplate_v5.SLDPRT]
2017-06-18 Created line cutter assembly and put in ENSR Baseplate and Lower Ring PDF Drawings
    [92620A605_HIGH-STRENGTH GRADE 8 STEEL CAP SCREW.SLDPRT, LINE CUTTER TUBE.SLDPRT, Line Cutter Assembly.SLDASM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]
2017-06-19 Fixed the main assembly; re-organized into '2.1' and '2.2'
    [91290A015.SLDPRT, 91735A021.SLDPRT, 91735A102.SLDPRT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]
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2017-06-19 Added motor part to the directory.
    [TURNIGY-2826-1240.SLDPRT]
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2017-06-19 Modified baseplate to increase thickness for M4s.
    [Baseplate_v5.SLDPRT, Bearing_Block(Custom).SLDPRT, Bracket_Motor.sldprt]
2017-06-23 CREATED DRAWINGS FOR NEW BASEPLATE AND LOWER RING
    [Baseplate V2.2.SLDDRW, Lower Ring V2.2.SLDDRW]
2017-07-01 started work on eNSR cap
    [eNSR_cap.1.SLDPRT, eNSR_cap.SLDPRT]
2017-07-01 This is a sketch for the ensr cap as discussed by marie and john and william
    [ASSY-RECOVERY.stp]
2017-07-06 Auto stash before merge of "master" and "origin/master"
    Countersunk hole in lower ring. Updated drawing
    [Lower Ring V2.2.SLDDRW, ring_lower.SLDPRT]
2017-07-06 Countersunk hole in lower ring. Updated drawing
    [Lower Ring V2.2.SLDDRW, ring_lower.SLDPRT]
2017-07-06 Updated baseplate and lower ring drawings
    more clearly showed holes.
    [Baseplate V2.2.SLDDRW, Lower Ring V2.2.SLDDRW, NSR lower ring.SLDDRW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]
2017-07-18 eNSR cap RD #1...ugh assembly mates, plz help..
    [ASSY-RECOVERY.SLDASM, BASEPLATE.sldprt, Baseplate_v5.SLDPRT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]
2017-07-25 ADDED MOUTING HOLES FOR ENSR CAP
    [Baseplate_v5.SLDPRT, Bearing_Block(Custom).SLDPRT]
2017-07-25 eNSR cap updates
    [eNSR_cap.2.SLDPRT]
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2017-07-26 eNSR cap changes
    [eNSR_cap.2.SLDPRT, eNSR_cap.2.STL]
2017-08-12 Drawings for motor bracket and bearing block.
    [Bearing_Block(Custom).SLDPRT]
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2017-08-13 Readding the eNSR cap.2
    [eNSR_cap.2.SLDPRT]
2017-08-24 chute housing update
    [Cup_Chute_Drogue^eNSR_v2.2.sldprt, Cylinder_Chute_Main^eNSR_v2.2.sldprt]
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2017-08-28 updated assembly
    [Cylinder_Chute_Main^eNSR_v2.2.sldprt]
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2017-08-31 updated ensr cap and created inserts to hold wave spring
    [Line Cutter Assembly.SLDASM, eNSR_cap.2 v2.STL, eNSR_cap.2.SLDPRT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]
2017-08-31 Created new ensr cap with ability to mount vesc
    [controller.SLDPRT, eNSR_cap.2 v2.STL, eNSR_cap.2 with vesc mounting.SLDPRT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]
2017-09-02 Made stl file for 3d printing nosecone cap
    [eNSR_cap.2 final.STL]
2017-09-10 Updated ensr design for motor encoder
    [4-40 3 8 in.SLDPRT, ACME_Screw.SLDPRT, Baseplate_v5.SLDPRT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]
2017-09-25 updated ensr cap for final assembly with cable clearance and hole position
    [Baseplate Modification.SLDDRW, Baseplate_v5.SLDPRT, Bracket_Motor.sldprt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]
2018-01-10 started making the test stand for motor/sensor testing
    [Bracket_Motor.sldprt, bottom.SLDPRT, eNSR_test_stand.SLDASM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]
2018-04-04 increased interface lip between drogue cup and main cylinder
    [Cylinder_Chute_Main^eNSR_v2.2.sldprt]
